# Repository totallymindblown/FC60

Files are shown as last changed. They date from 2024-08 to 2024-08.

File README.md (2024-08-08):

# **FC60**
A simple Feeder Controller for electric SMT-Feeders.
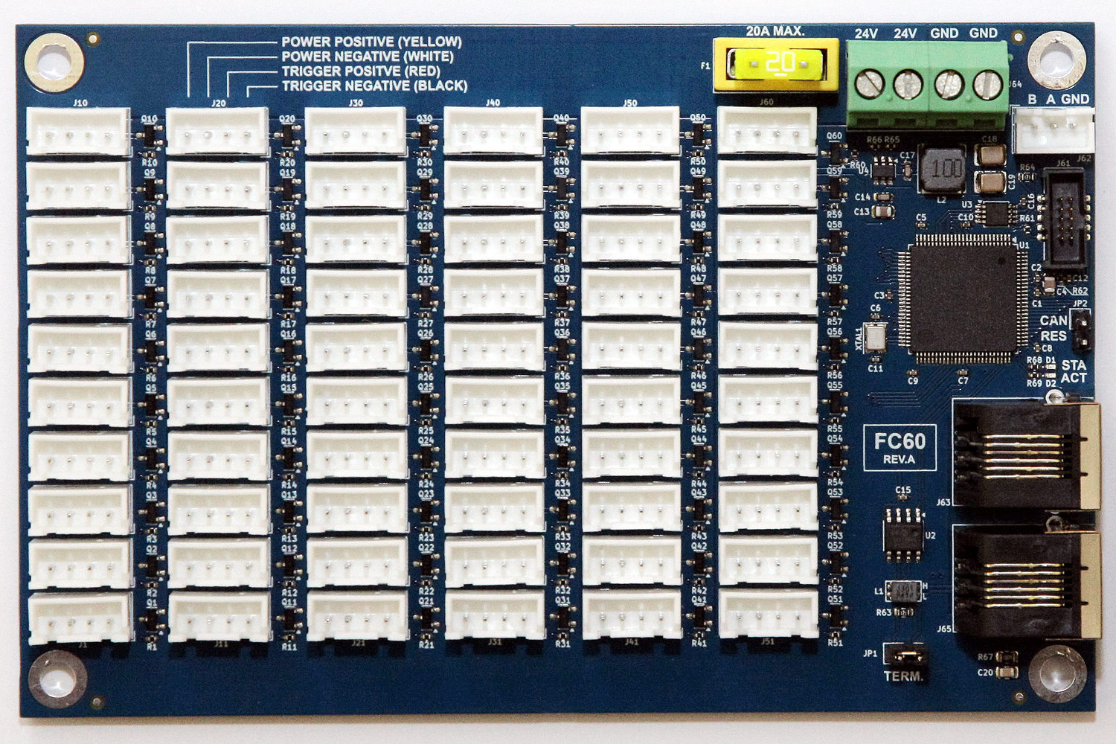
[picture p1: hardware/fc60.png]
FC60 Feeder Controller

## Specifications
* reliable Atmel SAMC21N18A MCU
* single 24V Power Supply
* max. 60 Feeders can be controlled with one Board
* CAN-FD Interface (compatible with MB6HC, MB6XD, etc.)
* optional RS485 Interface
## Hardware
The board has been designed with [Kicad 8.0.4](https://www.kicad.org).  
All schematics, design-files, gerbers and bom can be found in [hardware](/hardware/).
## Software
A Bootloader and Firmware for use with e.g. RFF 3.5 can be found in [Releases](http://github.com/totallymindblown/FC60/releases/latest).  

First the bootloader needs to be programmed with a suitable programmer (e.g. ATMEL-ICE, SEGGER J-Link, etc.) using the SWD-Interface J61 (10-pin 50mil connector), then the firmware can be uploaded from the mainboard. Since the MCU runs with 5V, the programmer must support this target voltage.
## How to Use
The feeders are each connected using connector J1..J60 and supplied with 24V. The trigger signal is provided by a short pulse (1 ms) to the control input of the feeder.
An appropriately dimensioned 24V switching power supply is connected to J64.

To be able to trigger the feeders, a single GPIO pin must be created for the FC60 using the following gcode example. The port number and CAN address are selected according to the application.

*_create Port 12 on FC60 with CAN address 24 :_* <b>`M950 P12 C"24.feeder"`</b>

The feeder is selected using <b>M42</b> with the <b>S</b> parameter, but it has here nothing to do with PWM. It is just a simple way on the FC60 to circumvent the RFF GPIO limit.  

*_trigger feeder number 1 :_* <b>`M42 P12 S1`</b>  

*_trigger feeder number 60 :_* <b>`M42 P12 S60`</b>  

The default CAN address of the FC60 is 124 which can be reset using JP2 (__CAN-RES__).  
CAN bus termination can be set with jumper JP1 (__TERM.__).

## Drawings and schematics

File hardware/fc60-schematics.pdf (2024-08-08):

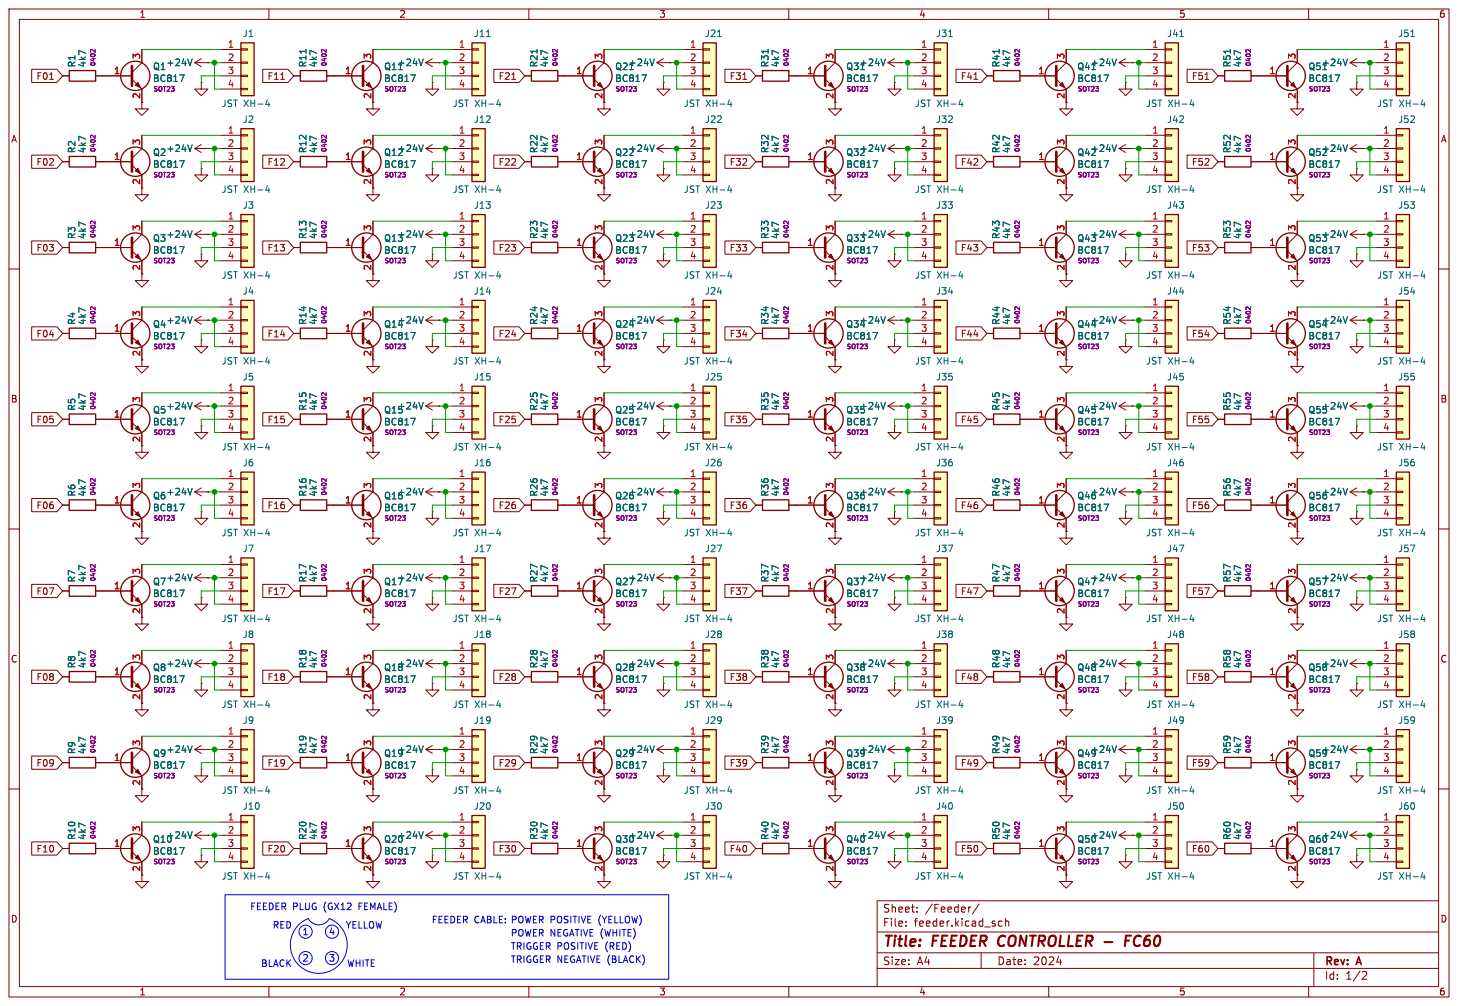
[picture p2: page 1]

File: feeder.kicad_sch Sheet: /Feeder/ 1234

POWER NEGATIVE (WHITE) FEEDER PLUG (GX12 FEMALE) 4 BLACK

Id: 1/2 Title: FEEDER CONTROLLER - FC60

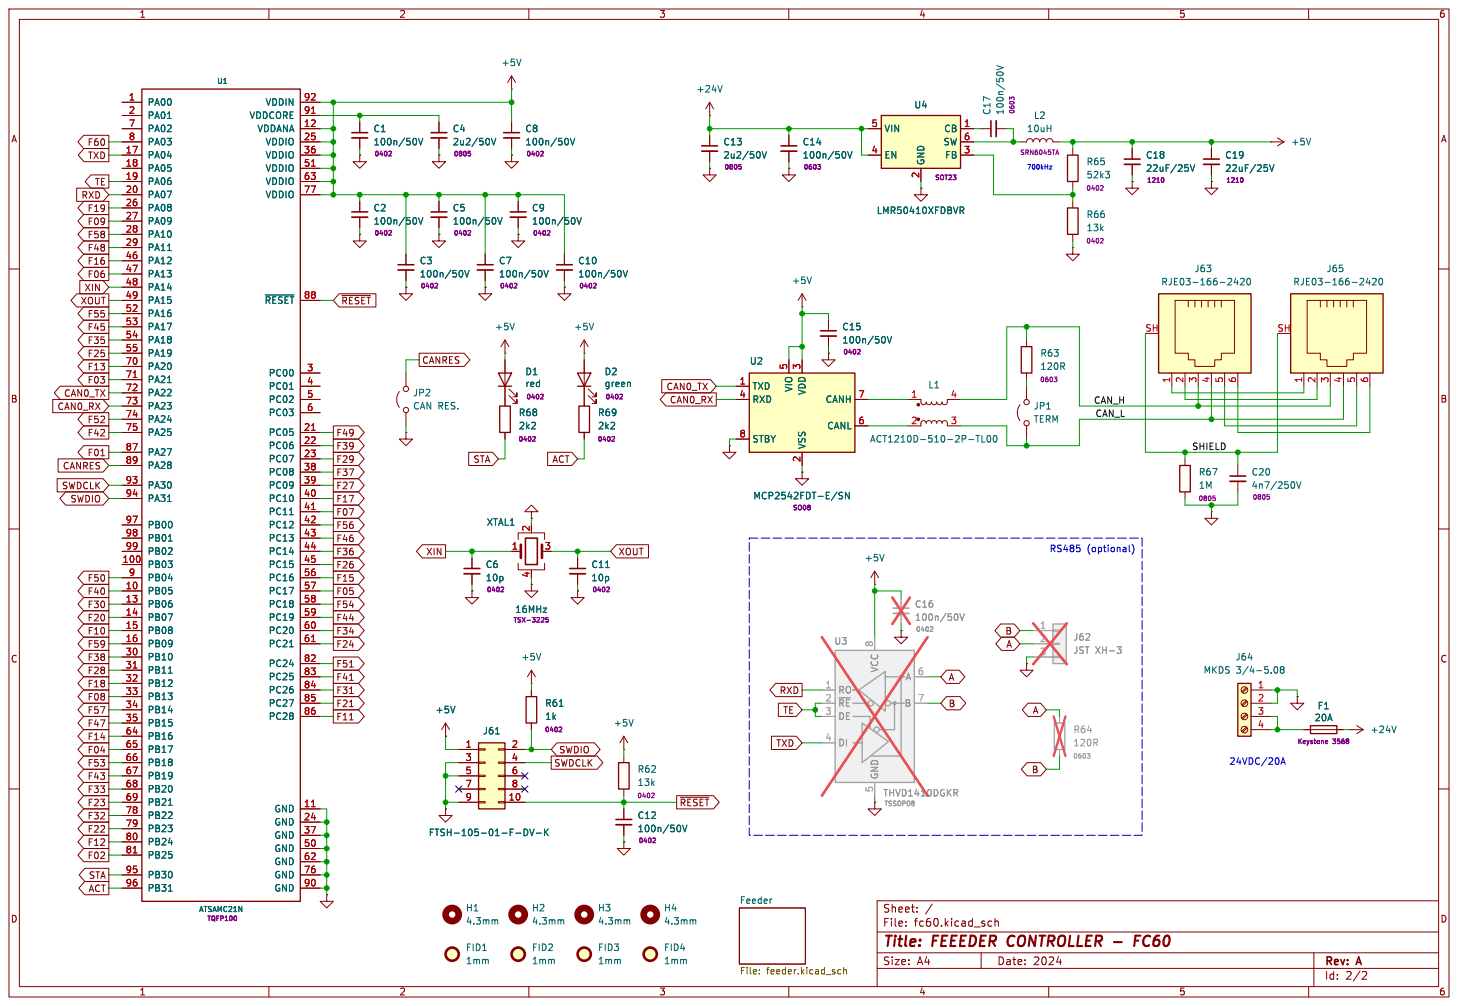
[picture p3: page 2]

2 FB 3 EN 4 VIN 5 SW 6 U4

2 FB 3 EN 4 VIN 5 SW 6 C13

5 CANL 6 CANH 7 STBY 8 U2MCP2542FDT-E/SN

File: fc60.kicad_sch Sheet: / Feeder File: feeder.kicad_sch

Id: 2/2 Title: FEEEDER CONTROLLER - FC60

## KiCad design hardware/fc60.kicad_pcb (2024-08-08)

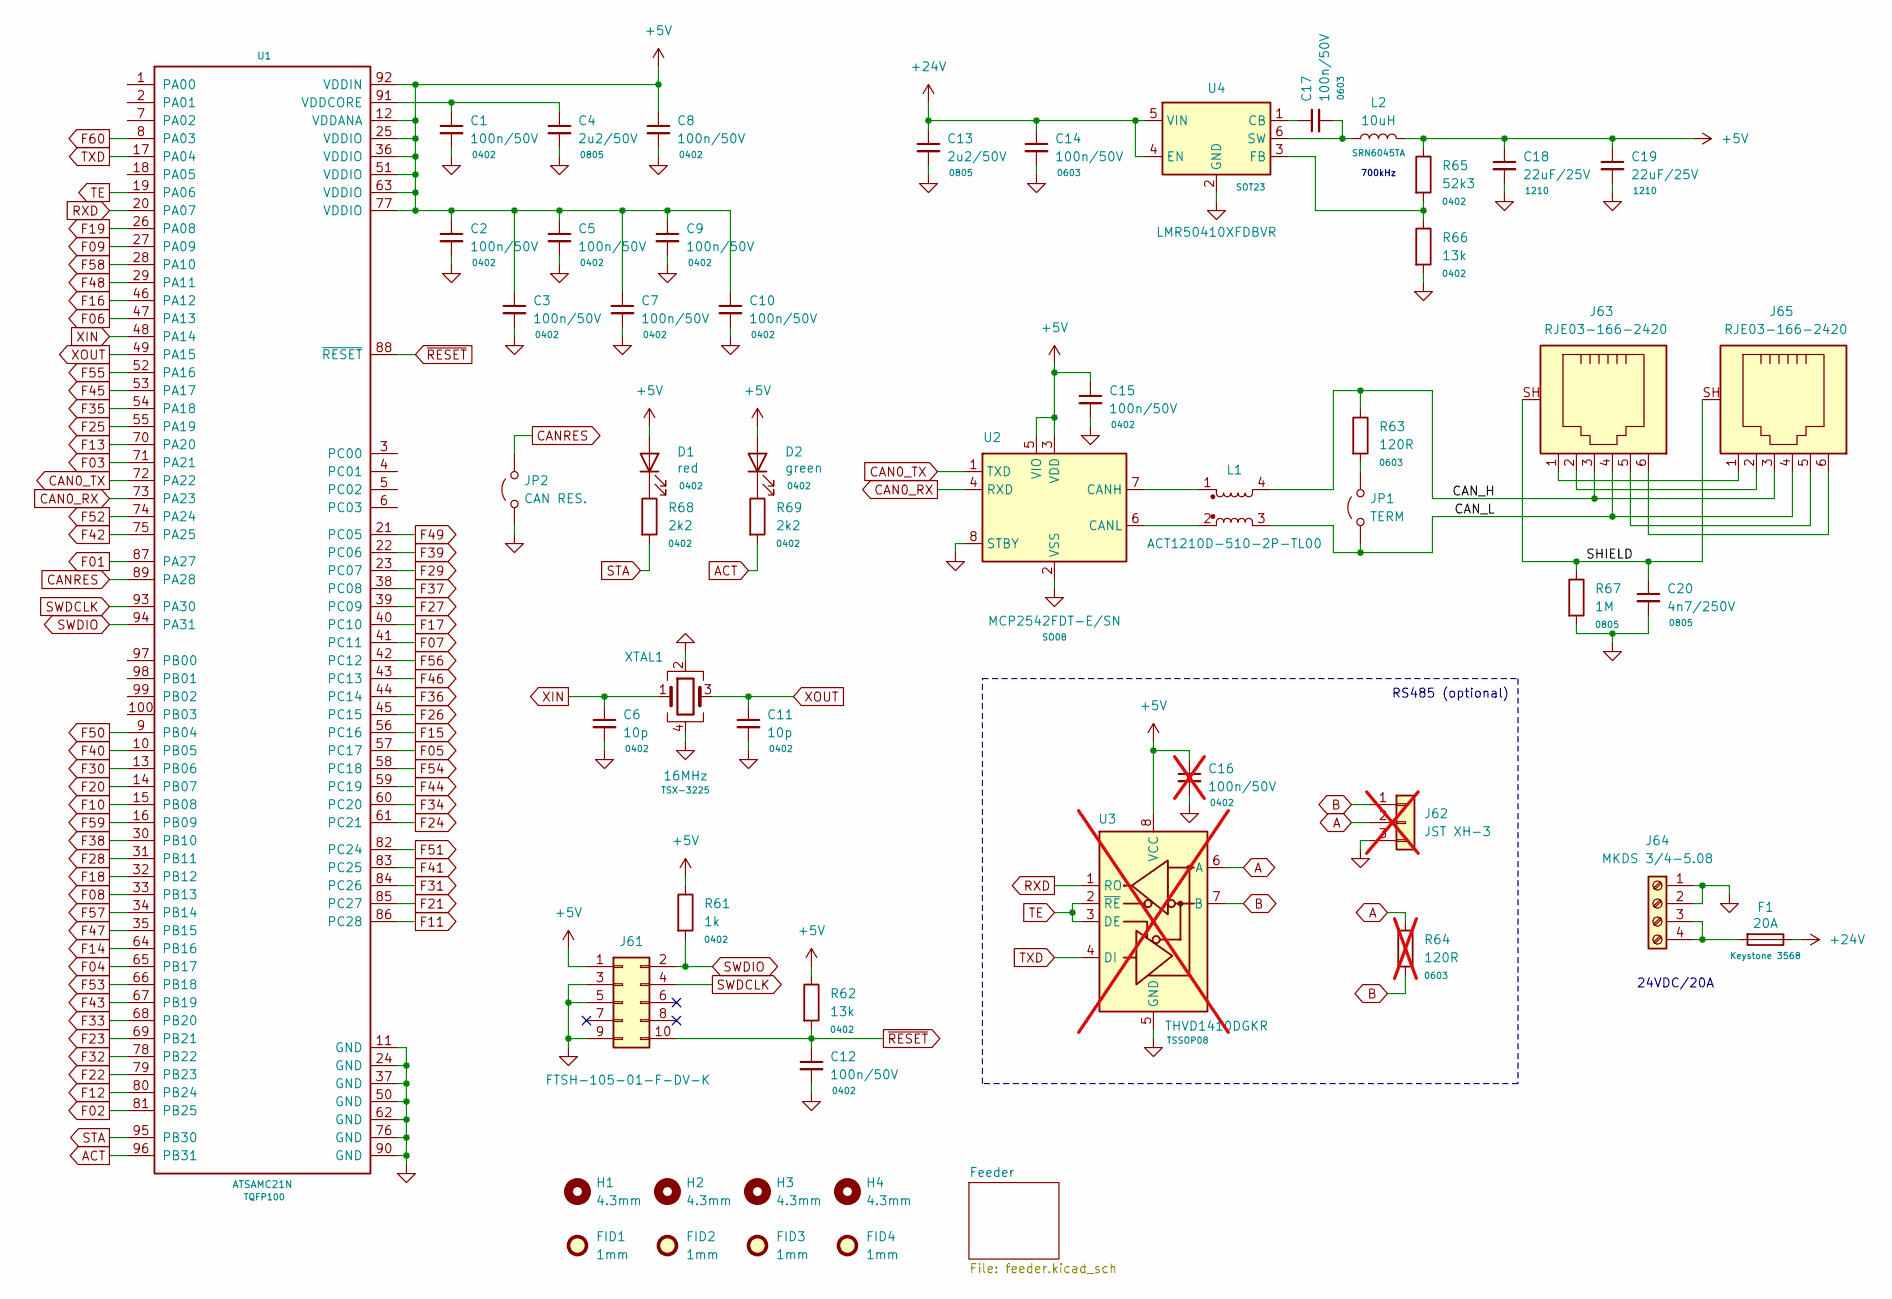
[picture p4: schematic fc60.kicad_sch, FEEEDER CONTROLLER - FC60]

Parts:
C1, C2, C3, C5, C7, C8, C9, C10, C12, C15: 100n/50V; C_0402_1005Metric
C4, C13: 2u2/50V; C_0805_2012Metric
C6, C11: 10p; C_0402_1005Metric
C14, C17: 100n/50V; C_0603_1608Metric
C16: 100n/50V; C_0402_1005Metric; not fitted
C18, C19: 22uF/25V; C_1210_3225Metric
C20: 4n7/250V; C_0805_2012Metric
D1: red; LED_0402_1005Metric
D2: green; LED_0402_1005Metric
F1: 20A; Fuseholder_Blade_Mini_Keystone_3568
FID1, FID2, FID3, FID4: 1mm; Fiducial_1mm_Mask2mm
H1, H2, H3, H4: 4.3mm; MountingHole_4.3mm_M4_ISO7380_Pad
J61: FTSH-105-01-F-DV-K; Samtec_SFH-105-01-F-D-K-TR
J62: JST XH-3; JST_XH_B3B-XH-A_1x03_P2.50mm_Vertical; not fitted
J63, J65: RJE03-166-2420; RJ25_Amphenol_RJE031662x20
J64: MKDS 3/4-5.08; TerminalBlock_Phoenix_MKDS-3-4-5.08_1x04_P5.08mm_Horizontal
JP1: TERM; PinHeader_1x02_P2.54mm_Vertical
JP2: CAN RES.; PinHeader_1x02_P2.54mm_Vertical
L1: ACT1210D-510-2P-TL00; L_CommonModeChoke_TDK_ACT1210D
L2: 10uH; L_Bourns_SRN6045TA
R61: 1k; R_0402_1005Metric
R62, R66: 13k; R_0402_1005Metric
R63: 120R; R_0603_1608Metric
R64: 120R; R_0603_1608Metric; not fitted
R65: 52k3; R_0402_1005Metric
R67: 1M; R_0805_2012Metric
R68, R69: 2k2; R_0402_1005Metric
U1: ATSAMC21N; TQFP-100_14x14mm_P0.5mm
U2: MCP2542FDT-E/SN; SO-8_3.9x4.9mm_P1.27mm
U3: THVD1410DGKR; TSSOP-8_3x3mm_P0.65mm; not fitted
U4: LMR50410XFDBVR; SOT-23-6
XTAL1: 16MHz; Crystal_SMD_SeikoEpson_TSX3225-4Pin_3.2x2.5mm

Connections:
+5V: C2.1, C3.1, C5.1, C7.1, C8.1, C9.1, C10.1, C15.1, C16.1, C18.1, C19.1, D1.2 (A), D2.2 (A), J61.1, L2.2, R61.1, R62.1, R65.1, U1.12 (VDDANA), U1.25 (VDDIO), U1.36 (VDDIO), U1.51 (VDDIO), U1.63 (VDDIO), U1.77 (VDDIO), U1.92 (VDDIN), U2.3 (VDD), U2.5 (VIO), U3.8 (VCC)
+24V: C13.1, C14.1, F1.1, U4.4 (EN), U4.5 (VIN); also elsewhere on the board
/CAN_H: J63.3, J65.3, L1.4, R63.1
/CAN_L: J63.4, J65.4, JP1.1 (A), L1.3
/SHIELD: C20.1, J63.SH, J65.SH, R67.1
A: J62.2, R64.1, U3.6 (A)
ACT: R69.2, U1.96 (PB31)
B: J62.1, R64.2, U3.7 (B)
CAN0_RX: U1.73 (PA23), U2.4 (RXD)
CAN0_TX: U1.72 (PA22), U2.1 (TXD)
CANRES: JP2.2 (B), U1.89 (PA28)
F01: U1.87 (PA27); also elsewhere on the board
F02: U1.81 (PB25); also elsewhere on the board
F03: U1.71 (PA21); also elsewhere on the board
F04: U1.65 (PB17); also elsewhere on the board
F05: U1.57 (PC17); also elsewhere on the board
F06: U1.47 (PA13); also elsewhere on the board
F07: U1.41 (PC11); also elsewhere on the board
F08: U1.33 (PB13); also elsewhere on the board
F09: U1.27 (PA09); also elsewhere on the board
F10: U1.15 (PB08); also elsewhere on the board
F11: U1.86 (PC28); also elsewhere on the board
F12: U1.80 (PB24); also elsewhere on the board
F13: U1.70 (PA20); also elsewhere on the board
F14: U1.64 (PB16); also elsewhere on the board
F15: U1.56 (PC16); also elsewhere on the board
F16: U1.46 (PA12); also elsewhere on the board
F17: U1.40 (PC10); also elsewhere on the board
F18: U1.32 (PB12); also elsewhere on the board
F19: U1.26 (PA08); also elsewhere on the board
F20: U1.14 (PB07); also elsewhere on the board
F21: U1.85 (PC27); also elsewhere on the board
F22: U1.79 (PB23); also elsewhere on the board
F23: U1.69 (PB21); also elsewhere on the board
F24: U1.61 (PC21); also elsewhere on the board
F25: U1.55 (PA19); also elsewhere on the board
F26: U1.45 (PC15); also elsewhere on the board
F27: U1.39 (PC09); also elsewhere on the board
F28: U1.31 (PB11); also elsewhere on the board
F29: U1.23 (PC07); also elsewhere on the board
F30: U1.13 (PB06); also elsewhere on the board
F31: U1.84 (PC26); also elsewhere on the board
F32: U1.78 (PB22); also elsewhere on the board
F33: U1.68 (PB20); also elsewhere on the board
F34: U1.60 (PC20); also elsewhere on the board
F35: U1.54 (PA18); also elsewhere on the board
F36: U1.44 (PC14); also elsewhere on the board
F37: U1.38 (PC08); also elsewhere on the board
F38: U1.30 (PB10); also elsewhere on the board
F39: U1.22 (PC06); also elsewhere on the board
F40: U1.10 (PB05); also elsewhere on the board
F41: U1.83 (PC25); also elsewhere on the board
F42: U1.75 (PA25); also elsewhere on the board
F43: U1.67 (PB19); also elsewhere on the board
F44: U1.59 (PC19); also elsewhere on the board
F45: U1.53 (PA17); also elsewhere on the board
F46: U1.43 (PC13); also elsewhere on the board
F47: U1.35 (PB15); also elsewhere on the board
F48: U1.29 (PA11); also elsewhere on the board
F49: U1.21 (PC05); also elsewhere on the board
F50: U1.9 (PB04); also elsewhere on the board
F51: U1.82 (PC24); also elsewhere on the board
F52: U1.74 (PA24); also elsewhere on the board
F53: U1.66 (PB18); also elsewhere on the board
F54: U1.58 (PC18); also elsewhere on the board
F55: U1.52 (PA16); also elsewhere on the board
F56: U1.42 (PC12); also elsewhere on the board
F57: U1.34 (PB14); also elsewhere on the board
F58: U1.28 (PA10); also elsewhere on the board
F59: U1.16 (PB09); also elsewhere on the board
F60: U1.8 (PA03); also elsewhere on the board
GND: C1.2, C2.2, C3.2, C4.2, C5.2, C6.2, C7.2, C8.2, C9.2, C10.2, C11.2, C12.2, C13.2, C14.2, C15.2, C16.2, C18.2, C19.2, C20.2, J61.3, J61.5, J61.9, J62.3, J64.1, J64.2, JP2.1 (A), R66.2, R67.2, U1.11 (GND), U1.24 (GND), U1.37 (GND), U1.50 (GND), U1.62 (GND), U1.76 (GND), U1.90 (GND), U2.2 (VSS), U2.8 (STBY), U3.5 (GND), U4.2 (GND), XTAL1.2, XTAL1.4; also elsewhere on the board
unnamed: D1.1 (K), R68.1
unnamed: D2.1 (K), R69.1
unnamed: J63.1, J65.1
unnamed: J63.2, J65.2
unnamed: J63.5, J65.5
unnamed: J63.6, J65.6
unnamed: F1.2, J64.3, J64.4
unnamed: JP1.2 (B), R63.2
unnamed: C1.1, C4.1, U1.91 (VDDCORE)
unnamed: L1.1, U2.7 (CANH)
unnamed: L1.2, U2.6 (CANL)
unnamed: C17.1, U4.1 (CB)
unnamed: R65.2, R66.1, U4.3 (FB)
unnamed: C17.2, L2.1, U4.6 (SW)
RXD: U1.20 (PA07), U3.1 (RO)
STA: R68.2, U1.95 (PB30)
SWDCLK: J61.4, U1.93 (PA30)
SWDIO: J61.2, R61.2, U1.94 (PA31)
TE: U1.19 (PA06), U3.2 (~RE), U3.3 (DE)
TXD: U1.17 (PA04), U3.4 (DI)
XIN: C6.1, U1.48 (PA14), XTAL1.1
XOUT: C11.1, U1.49 (PA15), XTAL1.3
~RESET: C12.1, J61.10, R62.2, U1.88 (~RESET)

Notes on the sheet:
24VDC/20A
RS485 (optional)
700kHz

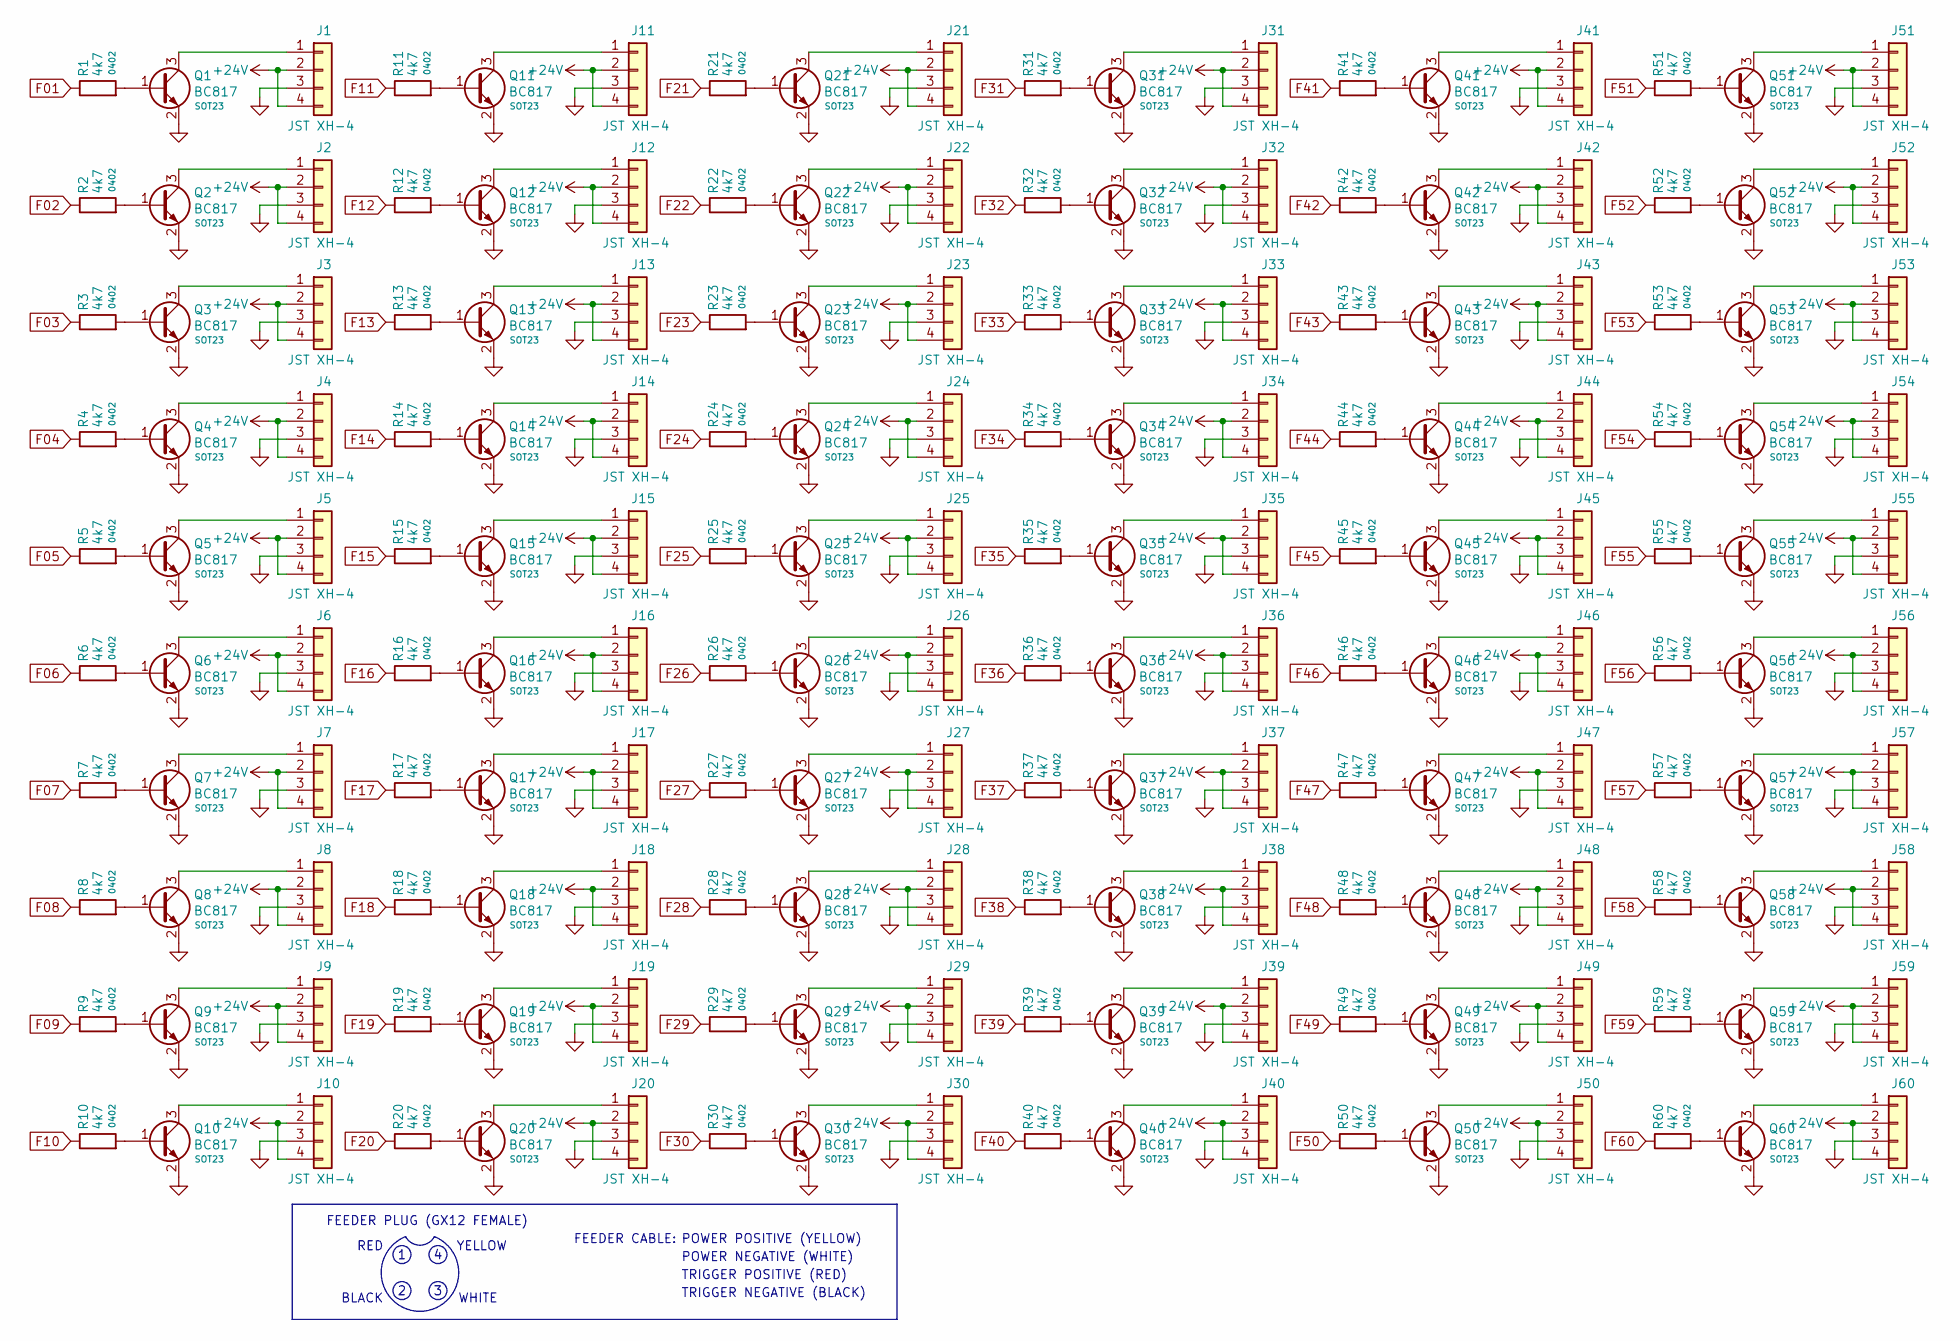
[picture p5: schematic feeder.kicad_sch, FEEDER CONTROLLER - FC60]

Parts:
J1, J2, J3, J4, J5, J6, J7, J8, J9, J10, J11, J12, J13, J14, J15, J16, J17, J18, J19, J20, J21, J22, J23, J24, J25, J26, J27, J28, J29, J30, J31, J32, J33, J34, J35, J36, J37, J38, J39, J40, J41, J42, J43, J44, J45, J46, J47, J48, J49, J50, J51, J52, J53, J54, J55, J56, J57, J58, J59, J60: JST XH-4; JST_XH_B4B-XH-A_1x04_P2.50mm_Vertical
Q1, Q2, Q3, Q4, Q5, Q6, Q7, Q8, Q9, Q10, Q11, Q12, Q13, Q14, Q15, Q16, Q17, Q18, Q19, Q20, Q21, Q22, Q23, Q24, Q25, Q26, Q27, Q28, Q29, Q30, Q31, Q32, Q33, Q34, Q35, Q36, Q37, Q38, Q39, Q40, Q41, Q42, Q43, Q44, Q45, Q46, Q47, Q48, Q49, Q50, Q51, Q52, Q53, Q54, Q55, Q56, Q57, Q58, Q59, Q60: BC817; SOT-23
R1, R2, R3, R4, R5, R6, R7, R8, R9, R10, R11, R12, R13, R14, R15, R16, R17, R18, R19, R20, R21, R22, R23, R24, R25, R26, R27, R28, R29, R30, R31, R32, R33, R34, R35, R36, R37, R38, R39, R40, R41, R42, R43, R44, R45, R46, R47, R48, R49, R50, R51, R52, R53, R54, R55, R56, R57, R58, R59, R60: 4k7; R_0402_1005Metric

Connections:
+24V: J1.2, J1.4, J2.2, J2.4, J3.2, J3.4, J4.2, J4.4, J5.2, J5.4, J6.2, J6.4, J7.2, J7.4, J8.2, J8.4, J9.2, J9.4, J10.2, J10.4, J11.2, J11.4, J12.2, J12.4, J13.2, J13.4, J14.2, J14.4, J15.2, J15.4, J16.2, J16.4, J17.2, J17.4, J18.2, J18.4, J19.2, J19.4, J20.2, J20.4, J21.2, J21.4, J22.2, J22.4, J23.2, J23.4, J24.2, J24.4, J25.2, J25.4, J26.2, J26.4, J27.2, J27.4, J28.2, J28.4, J29.2, J29.4, J30.2, J30.4, J31.2, J31.4, J32.2, J32.4, J33.2, J33.4, J34.2, J34.4, J35.2, J35.4, J36.2, J36.4, J37.2, J37.4, J38.2, J38.4, J39.2, J39.4, J40.2, J40.4, J41.2, J41.4, J42.2, J42.4, J43.2, J43.4, J44.2, J44.4, J45.2, J45.4, J46.2, J46.4, J47.2, J47.4, J48.2, J48.4, J49.2, J49.4, J50.2, J50.4, J51.2, J51.4, J52.2, J52.4, J53.2, J53.4, J54.2, J54.4, J55.2, J55.4, J56.2, J56.4, J57.2, J57.4, J58.2, J58.4, J59.2, J59.4, J60.2, J60.4; also elsewhere on the board
F01: R1.1; also elsewhere on the board
F02: R2.1; also elsewhere on the board
F03: R3.1; also elsewhere on the board
F04: R4.1; also elsewhere on the board
F05: R5.1; also elsewhere on the board
F06: R6.1; also elsewhere on the board
F07: R7.1; also elsewhere on the board
F08: R8.1; also elsewhere on the board
F09: R9.1; also elsewhere on the board
F10: R10.1; also elsewhere on the board
F11: R11.1; also elsewhere on the board
F12: R12.1; also elsewhere on the board
F13: R13.1; also elsewhere on the board
F14: R14.1; also elsewhere on the board
F15: R15.1; also elsewhere on the board
F16: R16.1; also elsewhere on the board
F17: R17.1; also elsewhere on the board
F18: R18.1; also elsewhere on the board
F19: R19.1; also elsewhere on the board
F20: R20.1; also elsewhere on the board
F21: R21.1; also elsewhere on the board
F22: R22.1; also elsewhere on the board
F23: R23.1; also elsewhere on the board
F24: R24.1; also elsewhere on the board
F25: R25.1; also elsewhere on the board
F26: R26.1; also elsewhere on the board
F27: R27.1; also elsewhere on the board
F28: R28.1; also elsewhere on the board
F29: R29.1; also elsewhere on the board
F30: R30.1; also elsewhere on the board
F31: R31.1; also elsewhere on the board
F32: R32.1; also elsewhere on the board
F33: R33.1; also elsewhere on the board
F34: R34.1; also elsewhere on the board
F35: R35.1; also elsewhere on the board
F36: R36.1; also elsewhere on the board
F37: R37.1; also elsewhere on the board
F38: R38.1; also elsewhere on the board
F39: R39.1; also elsewhere on the board
F40: R40.1; also elsewhere on the board
F41: R41.1; also elsewhere on the board
F42: R42.1; also elsewhere on the board
F43: R43.1; also elsewhere on the board
F44: R44.1; also elsewhere on the board
F45: R45.1; also elsewhere on the board
F46: R46.1; also elsewhere on the board
F47: R47.1; also elsewhere on the board
F48: R48.1; also elsewhere on the board
F49: R49.1; also elsewhere on the board
F50: R50.1; also elsewhere on the board
F51: R51.1; also elsewhere on the board
F52: R52.1; also elsewhere on the board
F53: R53.1; also elsewhere on the board
F54: R54.1; also elsewhere on the board
F55: R55.1; also elsewhere on the board
F56: R56.1; also elsewhere on the board
F57: R57.1; also elsewhere on the board
F58: R58.1; also elsewhere on the board
F59: R59.1; also elsewhere on the board
F60: R60.1; also elsewhere on the board
GND: J1.3, J2.3, J3.3, J4.3, J5.3, J6.3, J7.3, J8.3, J9.3, J10.3, J11.3, J12.3, J13.3, J14.3, J15.3, J16.3, J17.3, J18.3, J19.3, J20.3, J21.3, J22.3, J23.3, J24.3, J25.3, J26.3, J27.3, J28.3, J29.3, J30.3, J31.3, J32.3, J33.3, J34.3, J35.3, J36.3, J37.3, J38.3, J39.3, J40.3, J41.3, J42.3, J43.3, J44.3, J45.3, J46.3, J47.3, J48.3, J49.3, J50.3, J51.3, J52.3, J53.3, J54.3, J55.3, J56.3, J57.3, J58.3, J59.3, J60.3, Q1.2 (E), Q2.2 (E), Q3.2 (E), Q4.2 (E), Q5.2 (E), Q6.2 (E), Q7.2 (E), Q8.2 (E), Q9.2 (E), Q10.2 (E), Q11.2 (E), Q12.2 (E), Q13.2 (E), Q14.2 (E), Q15.2 (E), Q16.2 (E), Q17.2 (E), Q18.2 (E), Q19.2 (E), Q20.2 (E), Q21.2 (E), Q22.2 (E), Q23.2 (E), Q24.2 (E), Q25.2 (E), Q26.2 (E), Q27.2 (E), Q28.2 (E), Q29.2 (E), Q30.2 (E), Q31.2 (E), Q32.2 (E), Q33.2 (E), Q34.2 (E), Q35.2 (E), Q36.2 (E), Q37.2 (E), Q38.2 (E), Q39.2 (E), Q40.2 (E), Q41.2 (E), Q42.2 (E), Q43.2 (E), Q44.2 (E), Q45.2 (E), Q46.2 (E), Q47.2 (E), Q48.2 (E), Q49.2 (E), Q50.2 (E), Q51.2 (E), Q52.2 (E), Q53.2 (E), Q54.2 (E), Q55.2 (E), Q56.2 (E), Q57.2 (E), Q58.2 (E), Q59.2 (E), Q60.2 (E); also elsewhere on the board
unnamed: J1.1, Q1.3 (C)
unnamed: J2.1, Q2.3 (C)
unnamed: J3.1, Q3.3 (C)
unnamed: J4.1, Q4.3 (C)
unnamed: J5.1, Q5.3 (C)
unnamed: J6.1, Q6.3 (C)
unnamed: J7.1, Q7.3 (C)
unnamed: J8.1, Q8.3 (C)
unnamed: J9.1, Q9.3 (C)
unnamed: J10.1, Q10.3 (C)
unnamed: J11.1, Q11.3 (C)
unnamed: J12.1, Q12.3 (C)
unnamed: J13.1, Q13.3 (C)
unnamed: J14.1, Q14.3 (C)
unnamed: J15.1, Q15.3 (C)
unnamed: J16.1, Q16.3 (C)
unnamed: J17.1, Q17.3 (C)
unnamed: J18.1, Q18.3 (C)
unnamed: J19.1, Q19.3 (C)
unnamed: J20.1, Q20.3 (C)
unnamed: J21.1, Q21.3 (C)
unnamed: J22.1, Q22.3 (C)
unnamed: J23.1, Q23.3 (C)
unnamed: J24.1, Q24.3 (C)
unnamed: J25.1, Q25.3 (C)
unnamed: J26.1, Q26.3 (C)
unnamed: J27.1, Q27.3 (C)
unnamed: J28.1, Q28.3 (C)
unnamed: J29.1, Q29.3 (C)
unnamed: J30.1, Q30.3 (C)
unnamed: J31.1, Q31.3 (C)
unnamed: J32.1, Q32.3 (C)
unnamed: J33.1, Q33.3 (C)
unnamed: J34.1, Q34.3 (C)
unnamed: J35.1, Q35.3 (C)
unnamed: J36.1, Q36.3 (C)
unnamed: J37.1, Q37.3 (C)
unnamed: J38.1, Q38.3 (C)
unnamed: J39.1, Q39.3 (C)
unnamed: J40.1, Q40.3 (C)
unnamed: J41.1, Q41.3 (C)
unnamed: J42.1, Q42.3 (C)
unnamed: J43.1, Q43.3 (C)
unnamed: J44.1, Q44.3 (C)
unnamed: J45.1, Q45.3 (C)
unnamed: J46.1, Q46.3 (C)
unnamed: J47.1, Q47.3 (C)
unnamed: J48.1, Q48.3 (C)
unnamed: J49.1, Q49.3 (C)
unnamed: J50.1, Q50.3 (C)
unnamed: J51.1, Q51.3 (C)
unnamed: J52.1, Q52.3 (C)
unnamed: J53.1, Q53.3 (C)
unnamed: J54.1, Q54.3 (C)
unnamed: J55.1, Q55.3 (C)
unnamed: J56.1, Q56.3 (C)
unnamed: J57.1, Q57.3 (C)
unnamed: J58.1, Q58.3 (C)
unnamed: J59.1, Q59.3 (C)
unnamed: J60.1, Q60.3 (C)
unnamed: Q1.1 (B), R1.2
unnamed: Q2.1 (B), R2.2
unnamed: Q3.1 (B), R3.2
unnamed: Q4.1 (B), R4.2
unnamed: Q5.1 (B), R5.2
unnamed: Q6.1 (B), R6.2
unnamed: Q7.1 (B), R7.2
unnamed: Q8.1 (B), R8.2
unnamed: Q9.1 (B), R9.2
unnamed: Q10.1 (B), R10.2
unnamed: Q11.1 (B), R11.2
unnamed: Q12.1 (B), R12.2
unnamed: Q13.1 (B), R13.2
unnamed: Q14.1 (B), R14.2
unnamed: Q15.1 (B), R15.2
unnamed: Q16.1 (B), R16.2
unnamed: Q17.1 (B), R17.2
unnamed: Q18.1 (B), R18.2
unnamed: Q19.1 (B), R19.2
unnamed: Q20.1 (B), R20.2
unnamed: Q21.1 (B), R21.2
unnamed: Q22.1 (B), R22.2
unnamed: Q23.1 (B), R23.2
unnamed: Q24.1 (B), R24.2
unnamed: Q25.1 (B), R25.2
unnamed: Q26.1 (B), R26.2
unnamed: Q27.1 (B), R27.2
unnamed: Q28.1 (B), R28.2
unnamed: Q29.1 (B), R29.2
unnamed: Q30.1 (B), R30.2
unnamed: Q31.1 (B), R31.2
unnamed: Q32.1 (B), R32.2
unnamed: Q33.1 (B), R33.2
unnamed: Q34.1 (B), R34.2
unnamed: Q35.1 (B), R35.2
unnamed: Q36.1 (B), R36.2
unnamed: Q37.1 (B), R37.2
unnamed: Q38.1 (B), R38.2
unnamed: Q39.1 (B), R39.2
unnamed: Q40.1 (B), R40.2
unnamed: Q41.1 (B), R41.2
unnamed: Q42.1 (B), R42.2
unnamed: Q43.1 (B), R43.2
unnamed: Q44.1 (B), R44.2
unnamed: Q45.1 (B), R45.2
unnamed: Q46.1 (B), R46.2
unnamed: Q47.1 (B), R47.2
unnamed: Q48.1 (B), R48.2
unnamed: Q49.1 (B), R49.2
unnamed: Q50.1 (B), R50.2
unnamed: Q51.1 (B), R51.2
unnamed: Q52.1 (B), R52.2
unnamed: Q53.1 (B), R53.2
unnamed: Q54.1 (B), R54.2
unnamed: Q55.1 (B), R55.2
unnamed: Q56.1 (B), R56.2
unnamed: Q57.1 (B), R57.2
unnamed: Q58.1 (B), R58.2
unnamed: Q59.1 (B), R59.2
unnamed: Q60.1 (B), R60.2

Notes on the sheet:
FEEDER PLUG (GX12 FEMALE)
FEEDER CABLE:
POWER POSITIVE (YELLOW)
RED
TRIGGER NEGATIVE (BLACK)
TRIGGER POSITIVE (RED)
BLACK
YELLOW
POWER NEGATIVE (WHITE)
WHITE

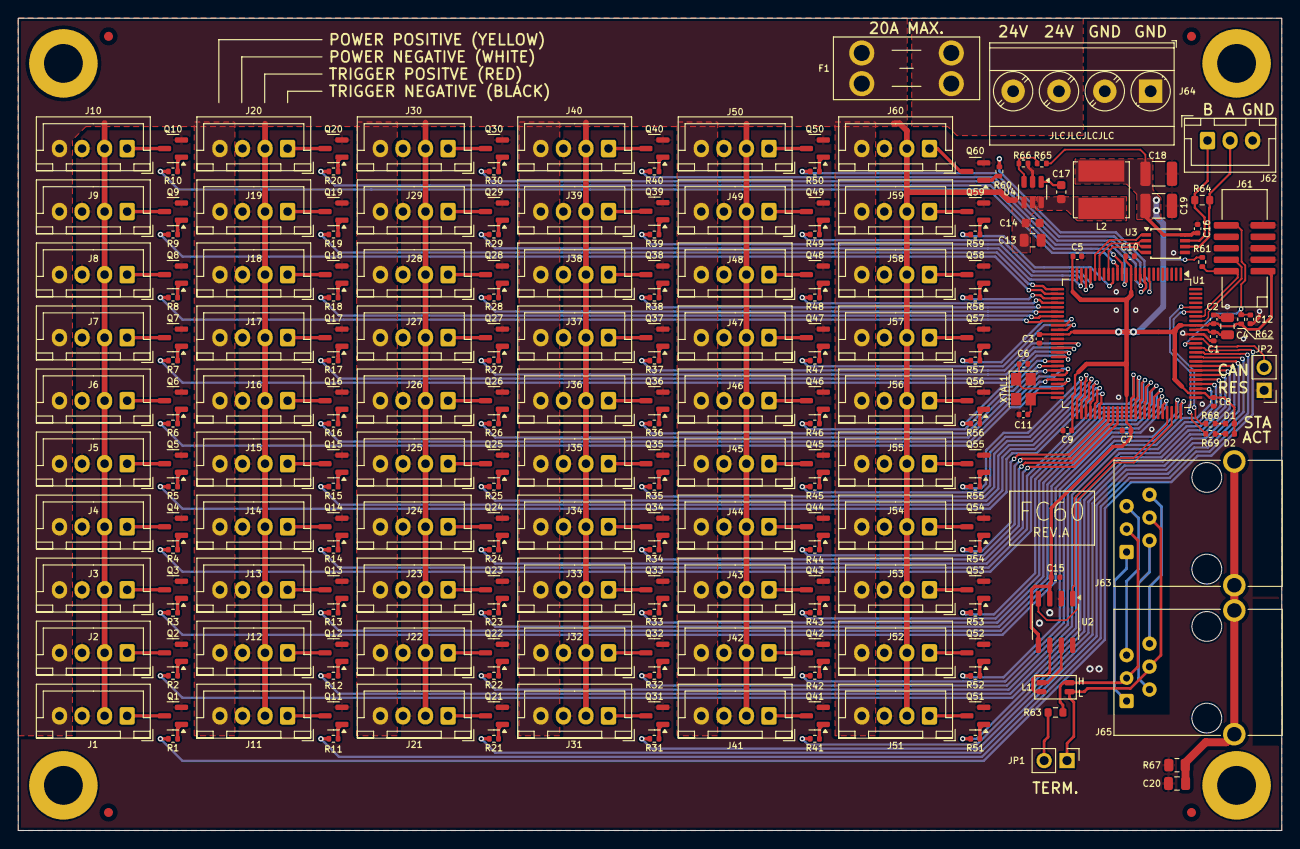
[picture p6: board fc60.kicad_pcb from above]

Board: 2 copper layers, 140.0 x 90.0 mm, 234 parts (0 on the bottom side), 215 nets.
